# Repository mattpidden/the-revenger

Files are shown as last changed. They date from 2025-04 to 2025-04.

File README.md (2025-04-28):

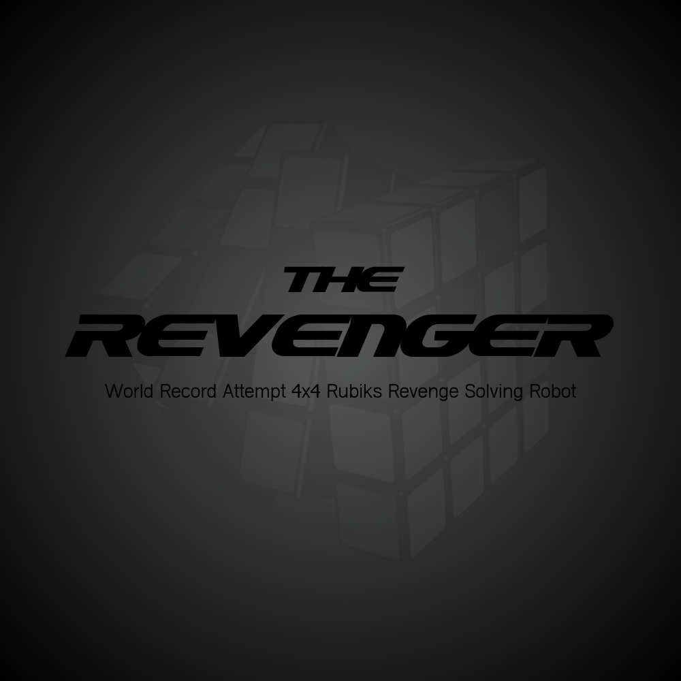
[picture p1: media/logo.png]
Banner Photo







# The Revenger - 4x4 Rubik’s Cube Solving Robot

This project presents the development of an efficient computational solver for the 4x4 Rubik's Cube and its implementation within a robotic system that achieves a world record solving time.

The approach uses a 2D array of integer facelet identifiers, which is the most suitable data structure for the 4x4 Rubik's Cube. This data structure is used in an 8 phase solving algorithm inspired by Tsai's method, and presented as the first C++ implementation of its kind. The approach is original yet closely based on Tsai's framework, offering a unique variation that prioritises practicality and performance. The 8 phase method achieves short solutions with an average move count of 67.79 moves in near real time. Additionally, novel research was conducted into optimising a computational solver to the characteristics and constraints of a specific robotic system, an area that has not been previously explored in existing literature. Unlike existing 4x4 solvers, this project is the only one accompanied by any explanation of the underlying theory and implementation, making it the first truly transparent and practical resource for 4x4 computational solving. The robot was designed and constructed from the ground up using fully custom parts and original architecture, independent of existing designs. The integration of the computational solver and robotic system achieved a solve time of 47.93 seconds, a 39.08% improvement over the current official world record. 

These results demonstrate that the robot, named 'The Revenger', has achieved an unofficial new world record time for solving the 4x4 Rubik's Cube. In due course the evidence will be submitted to Guinness World Records for review of official recognition.

A video demonstration of the robot is available on [YouTube](https://youtu.be/tE4DD7Fw6SM).

# Project Structure
```
code/ 
  solver/
  scanner/ 
  master/
  microcontroller/ 
parts/
  pcb/
media/
```

# Instructions
To run the 8 phase solver, first download the latest binary assets from [here](https://github.com/mattpidden/the-revenger/releases) and place them in the `code/solver` directory. Then type `make` to generate the compiled solver. Run `./solver -s` to solve a cube. It expects a 96 char input of the inital cube state.

To run the master program use `python main.py` inside the `code/master` directory. 

To run the computer vision scanning use `python manual_scan.py` inside the `code/scanner` directory. It is important that you calibrate your cameras first using `python calibrate_cameras.py`.

Upload the microcontroller code to an Arduino using the offical software.

# Parts List
Along with the parts provided that you will need to 3D print, there are also a selection of parts to source from elsewhere.
- Custom PCB (see files) (1 pcs)
- 360x20x20mm extrusion (14 pcs)
- 480x20x20mm extrusion (4 pcs)
- 150x20x20mm extrusion (5 pcs)
- 200x20x20mm extrusion (1 pcs)
- MGN12 100mm linear rail (5 pcs)
- MGN12 150mm linear rail (1 pcs)
- MGN12H sliding carriage blocks (6 pcs)
- Corner connections for 20x20mm extrusion
- 2GTx160x6mm timing belt (6 pcs)
- 2GTx6mm spool timing belt
- 2GT pulley, 20 teeth, 5mm bore (6 pcs)
- 2GT idler, 5mm bore (6 pcs)
- 2GT pulley, 40 teeth, 12mm bore, 28mm dia (4 pcs)
- 2GT pulley, 40 teeth, 5mm bore, 30mm dia (4 pcs)
- NEMA 17 0.65 Nm stepper motor (6 pcs)
- NEMA 17 0.45 Nm stepper motor (4 pcs)
- Endstop mechanical limit switch (6 pcs)
- 2 Lenovo Essential FHD webameras
- Arduino Due (1 pcs)
- DRV8825 stepper motor driver (10 pcs)
- TM1637 4 digit 7 segment display (1 pcs)
- DC buzzer (1 pcs)
- LED ring light (2 pcs)
- Capacitors
- Male and female header pins

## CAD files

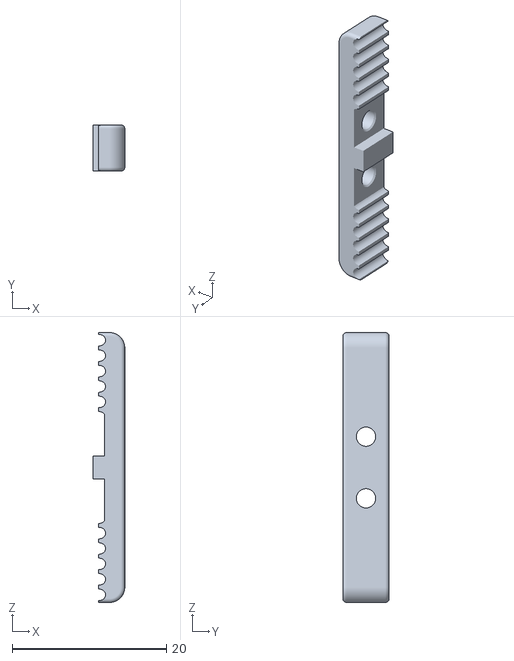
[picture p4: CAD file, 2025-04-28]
parts/4x4 Solver PRT_103-3-010325 - LA Inner Belt Joiner.STL
4.10 x 6.00 x 35.0

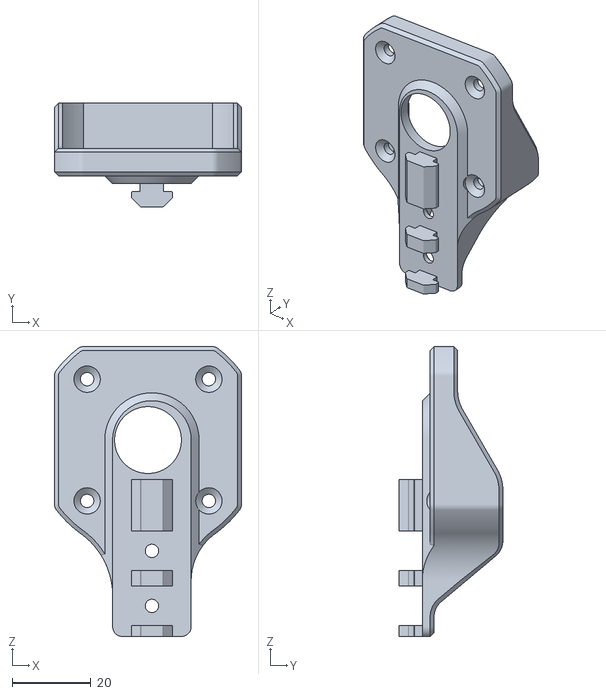
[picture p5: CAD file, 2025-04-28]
parts/4x4 Solver PRT_101-4-040325 - LA Motor Mount.STL
47.6 x 26.4 x 73.8

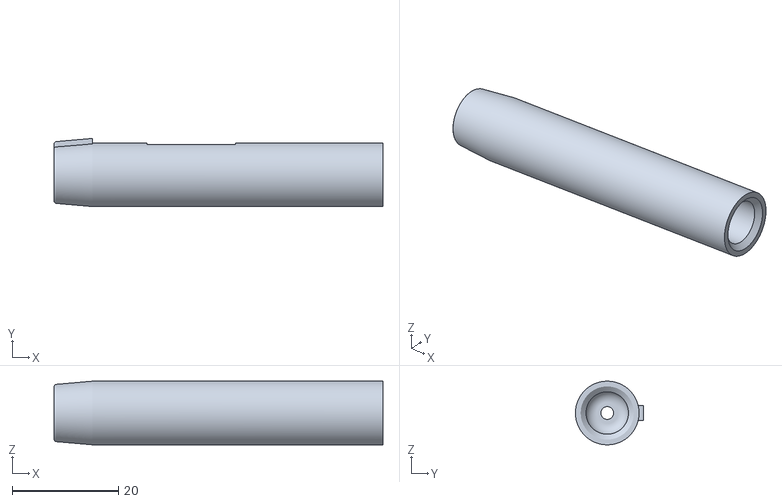
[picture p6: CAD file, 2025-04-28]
parts/4x4 Solver PRT_002-4-080325 - Claw Axel.STL
62.0 x 12.9 x 12.0

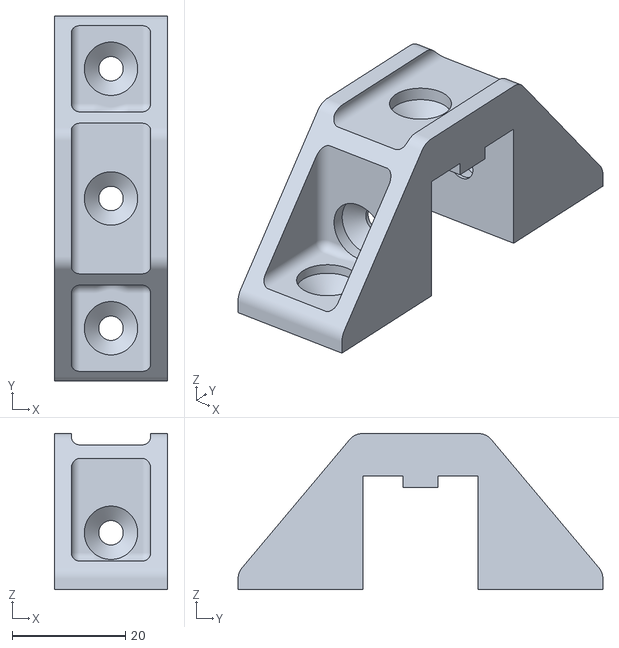
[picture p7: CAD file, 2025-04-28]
parts/4x4 Solver PRT_302-4-060325 - LA Frame Mount B.STL
20.0 x 64.3 x 27.5

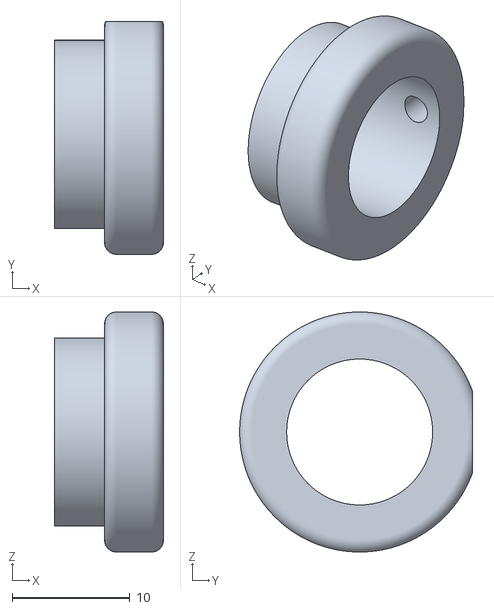
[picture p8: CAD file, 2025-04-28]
parts/4x4 Solver PRT_005-3-010325 - Axel Stopper.STL
9.25 x 19.8 x 20.4

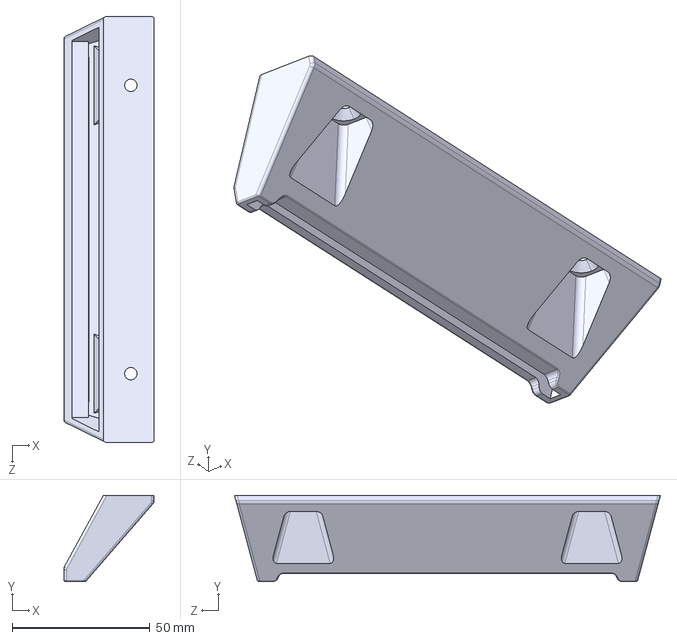
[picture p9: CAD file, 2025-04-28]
parts/4x4 Solver PRT_313-1-260325 - PCB Mount.STEP
32.9 x 31.2 x 154.7 mm

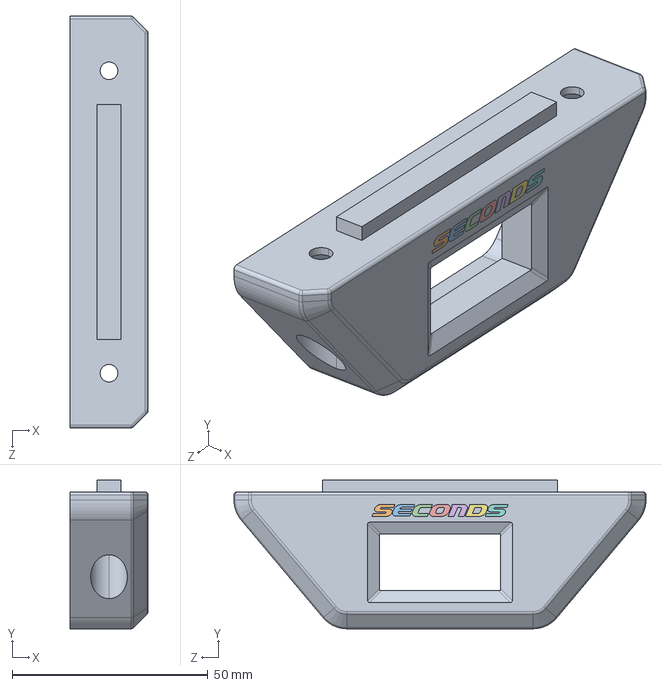
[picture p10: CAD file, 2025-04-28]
parts/4x4 Solver PRT_309--1-031025 - Clock Mount.STEP
20.0 x 38.0 x 105.3 mm

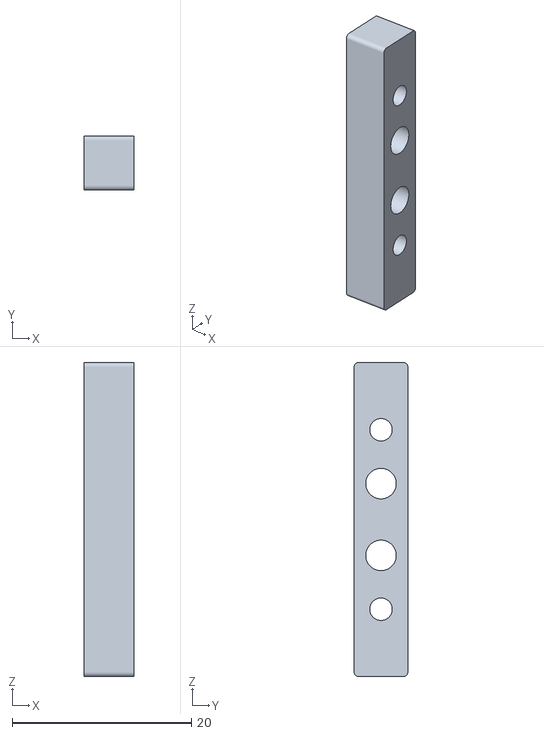
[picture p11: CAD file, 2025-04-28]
parts/4x4 Solver PRT_104-3-010325 - LA Outer Belt Joiner.STL
5.52 x 6.00 x 35.0

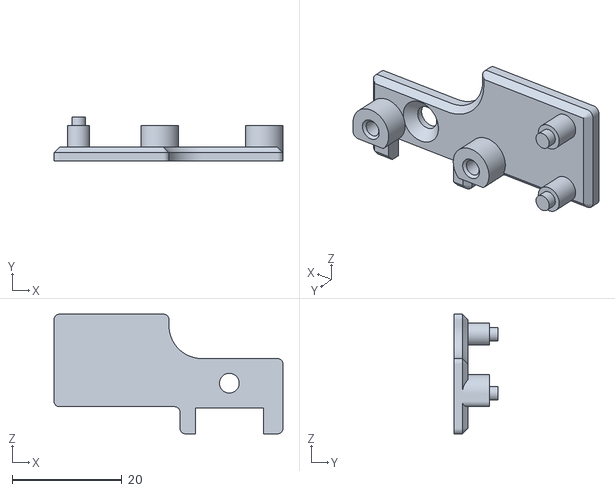
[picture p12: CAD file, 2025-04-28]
parts/4x4 Solver PRT_105-3-010325 - LA Switch Mount.STL
41.8 x 8.00 x 21.8

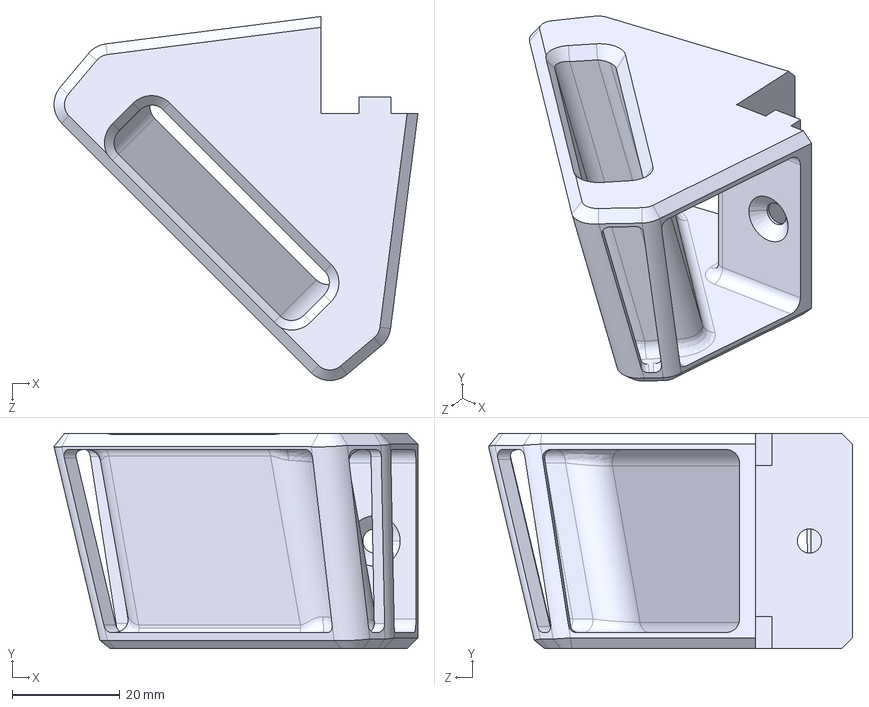
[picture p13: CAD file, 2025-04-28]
parts/4x4 Solver PRT_310-2-260325 - Camera clip.STEP
67.6 x 40.0 x 67.6 mm

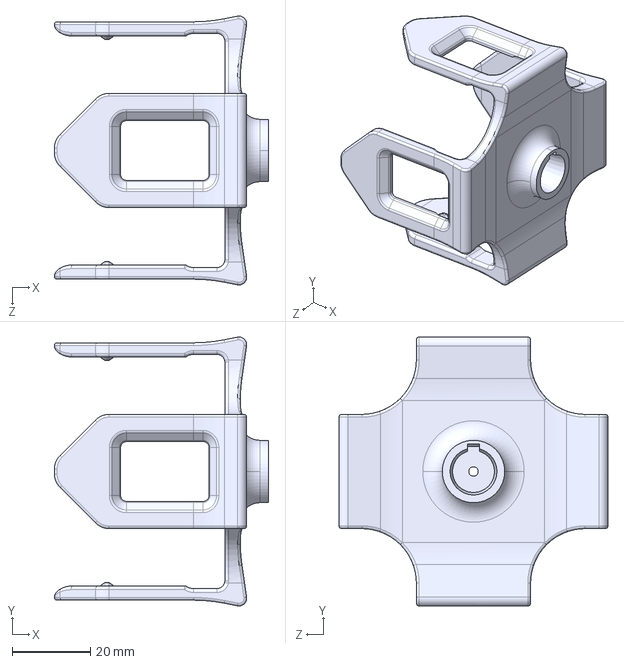
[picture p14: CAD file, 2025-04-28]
parts/4x4 Solver PRT_001-4-220425 - Claw.STEP
54.9 x 69.0 x 69.0 mm

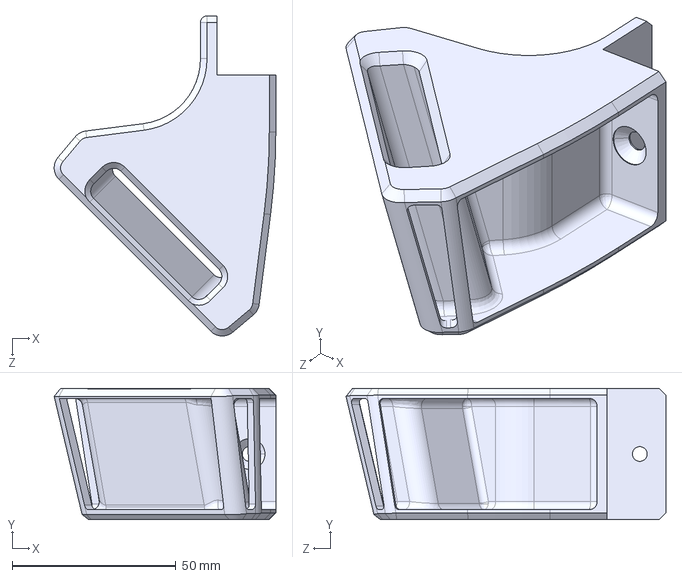
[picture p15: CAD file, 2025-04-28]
parts/4x4 Solver PRT_311-1-260325 - Camera clip B.STEP
67.6 x 40.0 x 97.6 mm

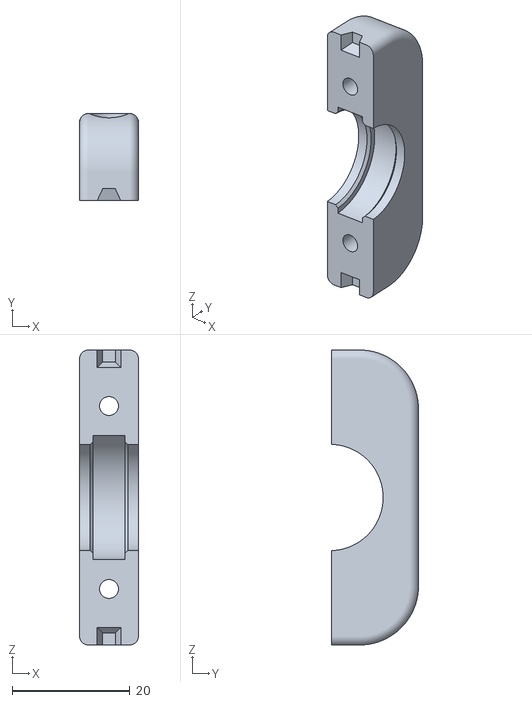
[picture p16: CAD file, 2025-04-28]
parts/4x4 Solver PRT_004-3-010325 - Bearing Cap.STL
10.00 x 14.8 x 50.0

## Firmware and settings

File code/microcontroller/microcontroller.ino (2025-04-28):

#include <AccelStepper.h>
#include <array>
#include "TM1637.h"

// ***************************************************
// ********************* PINS ************************
// ***************************************************
#define x_axis_1_la_dir 23
#define x_axis_1_la_step 30
#define x_axis_1_la_enable 13
#define x_axis_1_la_limit 32

#define x_axis_2_la_dir 25
#define x_axis_2_la_step 28
#define x_axis_2_la_enable 10
#define x_axis_2_la_limit 34

#define z_axis_1_la_dir 27
#define z_axis_1_la_step 26
#define z_axis_1_la_enable 9
#define z_axis_1_la_limit 40

#define z_axis_2_la_dir 29
#define z_axis_2_la_step 24
#define z_axis_2_la_enable 8
#define z_axis_2_la_limit 42

#define y_axis_1_la_dir 31
#define y_axis_1_la_step 22
#define y_axis_1_la_enable 33
#define y_axis_1_la_limit 36

#define y_axis_2_la_dir 53
#define y_axis_2_la_step 52
#define y_axis_2_la_enable 41
#define y_axis_2_la_limit 38

#define x_axis_1_claw_dir 5
#define x_axis_1_claw_step 6
#define x_axis_1_claw_enable 39

#define x_axis_2_claw_dir 15
#define x_axis_2_claw_step 14
#define x_axis_2_claw_enable 37

#define z_axis_1_claw_dir 49
#define z_axis_1_claw_step 48
#define z_axis_1_claw_enable 35

#define z_axis_2_claw_dir 51
#define z_axis_2_claw_step 50
#define z_axis_2_claw_enable 43

#define buzzer_pin 7
#define display_clock_pin 2
#define display_dio_pin 3




// ***************************************************
// **************** INITALISATION ********************
// ***************************************************
TM1637 digit_display(display_clock_pin, display_dio_pin);

struct LinearMotor {
    AccelStepper* stepper;
    int limit_pin;
    int enable_pin;
};

struct ClawMotor {
    AccelStepper* stepper;
    int enable_pin;
};

#define motorInterfaceType 1

AccelStepper x_axis_1_la_stepper(motorInterfaceType, x_axis_1_la_step, x_axis_1_la_dir);
AccelStepper x_axis_2_la_stepper(motorInterfaceType, x_axis_2_la_step, x_axis_2_la_dir);
AccelStepper z_axis_1_la_stepper(motorInterfaceType, z_axis_1_la_step, z_axis_1_la_dir);
AccelStepper z_axis_2_la_stepper(motorInterfaceType, z_axis_2_la_step, z_axis_2_la_dir);
AccelStepper y_axis_1_la_stepper(motorInterfaceType, y_axis_1_la_step, y_axis_1_la_dir);
AccelStepper y_axis_2_la_stepper(motorInterfaceType, y_axis_2_la_step, y_axis_2_la_dir);

AccelStepper x_axis_1_claw_stepper(motorInterfaceType, x_axis_1_claw_step, x_axis_1_claw_dir);
AccelStepper x_axis_2_claw_stepper(motorInterfaceType, x_axis_2_claw_step, x_axis_2_claw_dir);
AccelStepper z_axis_1_claw_stepper(motorInterfaceType, z_axis_1_claw_step, z_axis_1_claw_dir);
AccelStepper z_axis_2_claw_stepper(motorInterfaceType, z_axis_2_claw_step, z_axis_2_claw_dir);

LinearMotor x_axis_1_la = {&x_axis_1_la_stepper, x_axis_1_la_limit, x_axis_1_la_enable};
LinearMotor x_axis_2_la = {&x_axis_2_la_stepper, x_axis_2_la_limit, x_axis_2_la_enable};
LinearMotor z_axis_1_la = {&z_axis_1_la_stepper, z_axis_1_la_limit, z_axis_1_la_enable};
LinearMotor z_axis_2_la = {&z_axis_2_la_stepper, z_axis_2_la_limit, z_axis_2_la_enable};
LinearMotor y_axis_1_la = {&y_axis_1_la_stepper, y_axis_1_la_limit, y_axis_1_la_enable};
LinearMotor y_axis_2_la = {&y_axis_2_la_stepper, y_axis_2_la_limit, y_axis_2_la_enable};

ClawMotor x_axis_1_claw = {&x_axis_1_claw_stepper, x_axis_1_claw_enable};
ClawMotor x_axis_2_claw = {&x_axis_2_claw_stepper, x_axis_2_claw_enable};
ClawMotor z_axis_1_claw = {&z_axis_1_claw_stepper, z_axis_1_claw_enable};
ClawMotor z_axis_2_claw = {&z_axis_2_claw_stepper, z_axis_2_claw_enable};




// ***************************************************
// ****************** CONSTANTS **********************
// ***************************************************
std::array<LinearMotor, 6> la_motors = {x_axis_1_la, x_axis_2_la, z_axis_1_la, z_axis_2_la, y_axis_1_la, y_axis_2_la};
std::array<LinearMotor, 4> la_hub_motors = {x_axis_1_la, x_axis_2_la, z_axis_1_la, z_axis_2_la};
std::array<LinearMotor, 2> la_cg_motors = {y_axis_1_la, y_axis_2_la};
std::array<ClawMotor, 4> claw_motors = {x_axis_1_claw, x_axis_2_claw, z_axis_1_claw, z_axis_2_claw};

int steps_per_revolution = 200;
float pulley_circumfrence = 40.0;
float steps_per_mm = steps_per_revolution / pulley_circumfrence;

float linear_rail_distance = 62.2;
float depth_0_distance = 10.0;
float depth_1_distance = 33.6; 
float depth_2_distance = 47.2;
float depth_3_distance = 61.0;
float corner_grabber_engaged_distance = 56.5;
float corner_grabber_disengaged_distance = 42.0;

int depth_0_position = depth_0_distance * steps_per_mm;
int depth_1_position = depth_1_distance * steps_per_mm;
int depth_2_position = depth_2_distance * steps_per_mm;
int depth_3_position = depth_3_distance * steps_per_mm;
float corner_grabber_engaged_position = corner_grabber_engaged_distance * steps_per_mm;
float corner_grabber_disengaged_position = corner_grabber_disengaged_distance * steps_per_mm;

float linear_motor_max_speed = 40000.0;
float claw_motor_max_speed = 40000.0;
float linear_motor_acceleration = 8000.0;
float claw_motor_acceleration = 8000.0;





// ***************************************************
// ********************* SETUP ***********************
// ***************************************************
void setup() {
  Serial.begin(9600); 

  pinMode(x_axis_1_la_dir, OUTPUT); 
  pinMode(x_axis_1_la_step, OUTPUT); 
  pinMode(x_axis_2_la_dir, OUTPUT); 
  pinMode(x_axis_2_la_step, OUTPUT);
  pinMode(z_axis_1_la_dir, OUTPUT); 
  pinMode(z_axis_1_la_step, OUTPUT); 
  pinMode(z_axis_2_la_dir, OUTPUT); 
  pinMode(z_axis_2_la_step, OUTPUT); 
  pinMode(y_axis_1_la_dir, OUTPUT); 
  pinMode(y_axis_1_la_step, OUTPUT); 
  pinMode(y_axis_2_la_dir, OUTPUT); 
  pinMode(y_axis_2_la_step, OUTPUT); 
  pinMode(x_axis_1_claw_dir, OUTPUT); 
  pinMode(x_axis_1_claw_step, OUTPUT); 
  pinMode(x_axis_2_claw_dir, OUTPUT); 
  pinMode(x_axis_2_claw_step, OUTPUT); 
  pinMode(z_axis_1_claw_dir, OUTPUT); 
  pinMode(z_axis_1_claw_step, OUTPUT); 
  pinMode(z_axis_2_claw_dir, OUTPUT); 
  pinMode(z_axis_2_claw_step, OUTPUT); 
  
  pinMode(x_axis_1_la_enable, OUTPUT); 
  pinMode(x_axis_2_la_enable, OUTPUT); 
  pinMode(z_axis_1_la_enable, OUTPUT); 
  pinMode(z_axis_2_la_enable, OUTPUT); 
  pinMode(y_axis_1_la_enable, OUTPUT); 
  pinMode(y_axis_2_la_enable, OUTPUT); 
  pinMode(x_axis_1_claw_enable, OUTPUT); 
  pinMode(x_axis_2_claw_enable, OUTPUT); 
  pinMode(z_axis_1_claw_enable, OUTPUT); 
  pinMode(z_axis_2_claw_enable, OUTPUT); 
  pinMode(x_axis_1_la_limit, INPUT_PULLUP); 
  pinMode(x_axis_2_la_limit, INPUT_PULLUP); 
  pinMode(z_axis_1_la_limit, INPUT_PULLUP); 
  pinMode(z_axis_2_la_limit, INPUT_PULLUP); 
  pinMode(y_axis_1_la_limit, INPUT_PULLUP); 
  pinMode(y_axis_2_la_limit, INPUT_PULLUP); 
  pinMode(buzzer_pin, OUTPUT);
  
  digitalWrite(x_axis_1_la_enable, HIGH);
  digitalWrite(x_axis_2_la_enable, HIGH);
  digitalWrite(z_axis_1_la_enable, HIGH);
  digitalWrite(z_axis_2_la_enable, HIGH);
  digitalWrite(y_axis_1_la_enable, HIGH);
  digitalWrite(y_axis_2_la_enable, HIGH);
  digitalWrite(x_axis_1_claw_enable, HIGH);
  digitalWrite(x_axis_2_claw_enable, HIGH);
  digitalWrite(z_axis_1_claw_enable, HIGH);
  digitalWrite(z_axis_2_claw_enable, HIGH);

  for (LinearMotor &motor : la_motors) {
    motor.stepper->setMaxSpeed(linear_motor_max_speed);
    motor.stepper->setAcceleration(linear_motor_acceleration);
  }
  for (ClawMotor &motor : claw_motors) {
    motor.stepper->setMaxSpeed(claw_motor_max_speed);
    motor.stepper->setAcceleration(claw_motor_acceleration);
  }

  digit_display.init();
  digit_display.set(2);
  updateDisplay(micros(), micros());
  soundBuzzer();

}




// ***************************************************
// ******************* MAIN LOOP *********************
// ***************************************************
bool timer = false;
unsigned long start_time = micros(); 

void loop() {
  updateDisplay(start_time, micros());

  static String command = "";

  while (Serial.available() > 0) {
    char incoming_char = Serial.read();

    if (incoming_char == '\n' || incoming_char == '\r') {
      if (command.length() > 0) {
        apply_command(command);
        command = "";
      }
    } else {
      command += incoming_char;
    }
  }
}

void apply_command(String command) {
  if (command == "c") {
    calibrateLinearAcctuators(); 
  }
  else if (command == "C") {
    calibrateLinearAcctuatorsWithCube(); 
  }
  else if (command == "CY") {
    calibrateCornerGrabbers(); 
  }
  else if (command == "S") {
    move2LinearHub(y_axis_1_la, y_axis_2_la, corner_grabber_engaged_position, corner_grabber_engaged_position);
  }
  else if (command == "N") {
    soundBuzzer(); 
  }
  else if (command =="T") {
    timer = !timer;
    soundBuzzer(); 
    start_time = micros(); 
  }
  else if (command == "S1") {
    float linear_motor_max_speed = 40000.0;
    float claw_motor_max_speed = 40000.0;
    float linear_motor_acceleration = 8000.0;
    float claw_motor_acceleration = 8000.0;
    for (LinearMotor &motor : la_motors) {
      motor.stepper->setMaxSpeed(linear_motor_max_speed);
      motor.stepper->setAcceleration(linear_motor_acceleration);
    }
    for (ClawMotor &motor : claw_motors) {
      motor.stepper->setMaxSpeed(claw_motor_max_speed);
      motor.stepper->setAcceleration(claw_motor_acceleration);
    }
  }
  else if (command == "S2") {
    float linear_motor_max_speed = 60000.0;
    float claw_motor_max_speed = 60000.0;
    float linear_motor_acceleration = 20000.0;
    float claw_motor_acceleration = 20000.0;
    for (LinearMotor &motor : la_motors) {
      motor.stepper->setMaxSpeed(linear_motor_max_speed);
      motor.stepper->setAcceleration(linear_motor_acceleration);
    }
    for (ClawMotor &motor : claw_motors) {
      motor.stepper->setMaxSpeed(claw_motor_max_speed);
      motor.stepper->setAcceleration(claw_motor_acceleration);
    }
  }
  else if (command == "S3") {
    float linear_motor_max_speed = 80000.0;
    float claw_motor_max_speed = 80000.0;
    float linear_motor_acceleration = 60000.0;
    float claw_motor_acceleration = 35000.0;
    for (LinearMotor &motor : la_motors) {
      motor.stepper->setMaxSpeed(linear_motor_max_speed);
      motor.stepper->setAcceleration(linear_motor_acceleration);
    }
    for (ClawMotor &motor : claw_motors) {
      motor.stepper->setMaxSpeed(claw_motor_max_speed);
      motor.stepper->setAcceleration(claw_motor_acceleration);
    }
  }
  else if (command == "SPIN") {
    Serial.println(command);
    enableClaws(x_axis_1_claw, x_axis_2_claw);
    enableClaws(z_axis_1_claw, z_axis_2_claw);
    x_axis_1_claw.stepper->move(200 * 30);
    x_axis_2_claw.stepper->move(200 * 30);
    z_axis_1_claw.stepper->move(200 * 30);
    z_axis_2_claw.stepper->move(200 * 30);
    while (x_axis_1_claw.stepper->distanceToGo() != 0 || x_axis_2_claw.stepper->distanceToGo() != 0 || z_axis_1_claw.stepper->distanceToGo() != 0 || z_axis_2_claw.stepper->distanceToGo() != 0) {
      x_axis_1_claw.stepper->run();
      x_axis_2_claw.stepper->run();
      z_axis_1_claw.stepper->run();
      z_axis_2_claw.stepper->run();
    }
    disableClaws(x_axis_1_claw, x_axis_2_claw);
    disableClaws(z_axis_1_claw, z_axis_2_claw);
    return;
  }
  else if (command == "A") {
    adjustCornerGrabbers();
  }
  else if (command == "0") {
    move2LinearHub(x_axis_2_la, x_axis_1_la, depth_0_position, depth_0_position);
    move2LinearHub(z_axis_2_la, z_axis_1_la, depth_0_position, depth_0_position);
  }
  else if (command == "00") {
    move2LinearHub(x_axis_2_la, x_axis_1_la, 0, 0);
    move2LinearHub(z_axis_2_la, z_axis_1_la, 0, 0);
  }
  else if (command == "1") {
    move2LinearHub(x_axis_2_la, x_axis_1_la, depth_0_position, depth_2_position);
  }
  else if (command == "2") {
    move2LinearHub(x_axis_2_la, x_axis_1_la, depth_2_position, depth_2_position);
  }
  else if (command == "3") {
    move2LinearHub(x_axis_2_la, x_axis_1_la, depth_3_position, depth_1_position);
  }
  else if (command == "4") {
    move2LinearHub(z_axis_1_la, z_axis_2_la, depth_0_position, depth_0_position);
  }
  else if (command == "5") {
    move2LinearHub(z_axis_1_la, z_axis_2_la, depth_1_position, depth_3_position);
  }
  else if (command == "6") {
    move2LinearHub(z_axis_1_la, z_axis_2_la, depth_2_position, depth_2_position);
  }
  else if (command == "7") {
    move2LinearHub(z_axis_1_la, z_axis_2_la, depth_3_position, depth_1_position);
  }
  else if (command == "8") {
    move2LinearHub(y_axis_1_la, y_axis_2_la, corner_grabber_disengaged_position, corner_grabber_disengaged_position);
  }
  else if (command == "9") {
    move2LinearHub(y_axis_1_la, y_axis_2_la, corner_grabber_engaged_position, corner_grabber_engaged_position);
  }
  else if (command != "") {
    apply_move(command);
  }
  Serial.println(command);
}



// ***************************************************
// **************** OTHER FUNCTIONS ******************
// ***************************************************
void soundBuzzer() {
  digitalWrite(buzzer_pin, HIGH);
  delay(100);
  digitalWrite(buzzer_pin, LOW);
}

void updateDisplay(unsigned long startTime, unsigned long endTime) {
  if (timer) {
    unsigned long durationMicroseconds = endTime - startTime;
    float durationMilliseconds = durationMicroseconds / 1000.0;
    float durationSeconds = durationMicroseconds / 1000000.0;
    int totalSeconds = (int)durationSeconds;
    int minutes = totalSeconds / 60;
    int seconds = totalSeconds % 60;
    int hundredths = ((int)durationMilliseconds % 1000) / 10;
    int8_t displayValues[4];
    if (totalSeconds >= 60) {
      displayValues[0] = static_cast<int8_t>(minutes / 10);
      displayValues[1] = static_cast<int8_t>(minutes % 10);
      displayValues[2] = static_cast<int8_t>(seconds / 10);
      displayValues[3] = static_cast<int8_t>(seconds % 10);
    } else {
      displayValues[0] = static_cast<int8_t>(totalSeconds / 10);
      displayValues[1] = static_cast<int8_t>(totalSeconds % 10);
      displayValues[2] = static_cast<int8_t>(hundredths / 10);
      displayValues[3] = static_cast<int8_t>(hundredths % 10);
    }
    digit_display.point(POINT_ON);
    digit_display.display(displayValues);
  }
}


void resetDisplay() {
  digit_display.clearDisplay();
  digit_display.point(POINT_OFF);
}

void calibrateLinearAcctuators() {
  for (LinearMotor &motor : la_motors) {
    digitalWrite(motor.enable_pin, LOW);
    while (digitalRead(motor.limit_pin) == HIGH) { 
      motor.stepper->move(-1); 
      motor.stepper->run();
      delay(10);
    }
    motor.stepper->stop();
    motor.stepper->setCurrentPosition(0);
    motor.stepper->moveTo(depth_0_position);
    motor.stepper->runToPosition();
    digitalWrite(motor.enable_pin, HIGH);
  }
  moveLinearHub(y_axis_2_la, corner_grabber_engaged_position);
}

void calibrateLinearAcctuatorsWithCube() {
  for (LinearMotor &motor : la_hub_motors) {
    digitalWrite(motor.enable_pin, LOW);
    while (digitalRead(motor.limit_pin) == HIGH) { 
      motor.stepper->move(-1); 
      motor.stepper->run();
      delay(10);
    }
    motor.stepper->stop();
    motor.stepper->setCurrentPosition(0);
    motor.stepper->moveTo(depth_0_position);
    motor.stepper->runToPosition();
    digitalWrite(motor.enable_pin, HIGH);
  }
  move2LinearHub(x_axis_1_la, x_axis_2_la, depth_2_position, depth_2_position);
  calibrateCornerGrabbers();
  move2LinearHub(x_axis_1_la, x_axis_2_la, depth_0_position, depth_0_position);
}

void calibrateCornerGrabbers() {
  for (LinearMotor &motor : la_cg_motors) {
    digitalWrite(motor.enable_pin, LOW);
    while (digitalRead(motor.limit_pin) == HIGH) { 
      motor.stepper->move(-1); 
      motor.stepper->run();
      delay(10);
    }
    motor.stepper->stop();
    motor.stepper->setCurrentPosition(0);
    digitalWrite(motor.enable_pin, HIGH);
  }
  move2LinearHub(y_axis_1_la, y_axis_2_la, corner_grabber_engaged_position, corner_grabber_engaged_position);
}

void moveLinearHub(LinearMotor motor, int position) {
  updateDisplay(start_time, micros());
  digitalWrite(motor.enable_pin, LOW);
  motor.stepper->moveTo(position);
  motor.stepper->runToPosition();
  digitalWrite(motor.enable_pin, HIGH);
}

void move2LinearHub(LinearMotor motor1, LinearMotor motor2, int position1, int position2) {
  updateDisplay(start_time, micros());
  digitalWrite(motor1.enable_pin, LOW);
  digitalWrite(motor2.enable_pin, LOW);
  motor1.stepper->moveTo(position1);
  motor2.stepper->moveTo(position2);
  while (motor1.stepper->distanceToGo() != 0 || motor2.stepper->distanceToGo() != 0) {
    motor1.stepper->run();
    motor2.stepper->run();
  }
  digitalWrite(motor1.enable_pin, HIGH);
  digitalWrite(motor2.enable_pin, HIGH);
}

void adjustCornerGrabbers() {
  digitalWrite(y_axis_1_la.enable_pin, LOW);
  digitalWrite(y_axis_2_la.enable_pin, LOW);
  y_axis_2_la.stepper->move(5);
  y_axis_2_la.stepper->runToPosition();
  digitalWrite(y_axis_1_la.enable_pin, HIGH);
  digitalWrite(y_axis_2_la.enable_pin, HIGH);
}

void enableClaws(ClawMotor claw1, ClawMotor claw2) {
  updateDisplay(start_time, micros());
  digitalWrite(claw1.enable_pin, LOW);
  digitalWrite(claw2.enable_pin, LOW);
}

void disableClaws(ClawMotor claw1, ClawMotor claw2) {
  updateDisplay(start_time, micros());
  digitalWrite(claw1.enable_pin, HIGH);
  digitalWrite(claw2.enable_pin, HIGH);
}

void rotateClaw(ClawMotor active_claw, int turns) {
  updateDisplay(start_time, micros());
  active_claw.stepper->move(50 * turns);
  while (active_claw.stepper->distanceToGo() != 0) {
    active_claw.stepper->run();
  }
}

void rotate2Claws(ClawMotor claw1, ClawMotor claw2, int turns) {
  updateDisplay(start_time, micros());
  claw1.stepper->move(50 * turns);
  claw2.stepper->move(50 * turns);
  while (claw1.stepper->distanceToGo() != 0 || claw2.stepper->distanceToGo() != 0) {
    claw1.stepper->run();
    claw2.stepper->run();
  }
}




// ***************************************************
// **************** MOVE FUNCTIONS *******************
// ***************************************************

void apply_move(String m) {
  if      (m == "R")   R_move(1); 
  else if (m == "R2")  R_move(2);
  else if (m == "R'")  R_move(-1);
  else if (m == "L")   L_move(1); 
  else if (m == "L2")  L_move(2);
  else if (m == "L'")  L_move(-1);
  else if (m == "F")   F_move(1); 
  else if (m == "F2")  F_move(2);
  else if (m == "F'")  F_move(-1);
  else if (m == "B")   B_move(1); 
  else if (m == "B2")  B_move(2);
  else if (m == "B'")  B_move(-1);
  else if (m == "U")   U_move(1); 
  else if (m == "U2")  U_move(2);
  else if (m == "U'")  U_move(-1);
  else if (m == "D")   D_move(1); 
  else if (m == "D2")  D_move(2);
  else if (m == "D'")  D_move(-1);
  else if (m == "r")   r_move(1); 
  else if (m == "r2")  r_move(2);
  else if (m == "r'")  r_move(-1);
  else if (m == "l")   l_move(1); 
  else if (m == "l2")  l_move(2);
  else if (m == "l'")  l_move(-1);
  else if (m == "f")   f_move(1); 
  else if (m == "f2")  f_move(2);
  else if (m == "f'")  f_move(-1);
  else if (m == "b")   b_move(1); 
  else if (m == "b2")  b_move(2);
  else if (m == "b'")  b_move(-1);
  else if (m == "u")   u_move(1); 
  else if (m == "u2")  u_move(2);
  else if (m == "u'")  u_move(-1);
  else if (m == "d")   d_move(1); 
  else if (m == "d2")  d_move(2);
  else if (m == "d'")  d_move(-1);
  else if (m == "Rw")  Rw_move(1); 
  else if (m == "Rw2") Rw_move(2);
  else if (m == "Rw'") Rw_move(-1);
  else if (m == "Lw")  Lw_move(1); 
  else if (m == "Lw2") Lw_move(2);
  else if (m == "Lw'") Lw_move(-1);
  else if (m == "Fw")  Fw_move(1); 
  else if (m == "Fw2") Fw_move(2);
  else if (m == "Fw'") Fw_move(-1);
  else if (m == "Bw")  Bw_move(1); 
  else if (m == "Bw2") Bw_move(2);
  else if (m == "Bw'") Bw_move(-1);
  else if (m == "Uw")  Uw_move(1); 
  else if (m == "Uw2") Uw_move(2);
  else if (m == "Uw'") Uw_move(-1);
  else if (m == "Dw")  Dw_move(1); 
  else if (m == "Dw2") Dw_move(2);
  else if (m == "Dw'") Dw_move(-1);
}

void R_move(int turns) {
  move2LinearHub(z_axis_1_la, z_axis_2_la, depth_0_position, depth_0_position);
  move2LinearHub(x_axis_1_la, x_axis_2_la, depth_3_position, depth_1_position);
  enableClaws(x_axis_2_claw, x_axis_1_claw);
  move2LinearHub(y_axis_1_la, y_axis_2_la, corner_grabber_disengaged_position, corner_grabber_disengaged_position);
  rotateClaw(x_axis_2_claw, turns);
  move2LinearHub(y_axis_1_la, y_axis_2_la, corner_grabber_engaged_position, corner_grabber_engaged_position);
  adjustCornerGrabbers();
  disableClaws(x_axis_2_claw, x_axis_1_claw);
}

void L_move(int turns) {
  move2LinearHub(z_axis_1_la, z_axis_2_la, depth_0_position, depth_0_position);
  move2LinearHub(x_axis_1_la, x_axis_2_la, depth_1_position, depth_3_position);
  enableClaws(x_axis_1_claw, x_axis_2_claw);
  move2LinearHub(y_axis_1_la, y_axis_2_la, corner_grabber_disengaged_position, corner_grabber_disengaged_position);
  rotateClaw(x_axis_1_claw, -turns);
  move2LinearHub(y_axis_1_la, y_axis_2_la, corner_grabber_engaged_position, corner_grabber_engaged_position);
  adjustCornerGrabbers();
  disableClaws(x_axis_1_claw, x_axis_2_claw);
}

void F_move(int turns) {
  move2LinearHub(x_axis_1_la, x_axis_2_la, depth_0_position, depth_0_position);
  move2LinearHub(z_axis_1_la, z_axis_2_la, depth_1_position, depth_3_position);
  enableClaws(z_axis_1_claw, z_axis_2_claw);
  move2LinearHub(y_axis_1_la, y_axis_2_la, corner_grabber_disengaged_position, corner_grabber_disengaged_position);
  rotateClaw(z_axis_1_claw, turns);
  move2LinearHub(y_axis_1_la, y_axis_2_la, corner_grabber_engaged_position, corner_grabber_engaged_position);
  adjustCornerGrabbers();
  disableClaws(z_axis_1_claw, z_axis_2_claw);
}
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

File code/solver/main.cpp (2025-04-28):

#include <vector>
#include <limits>
#include <iostream>
#include <fstream>
#include <unordered_map>
#include <functional>
#include <chrono>
#include "cube.h"
#include "BooPHF.h"
using namespace boomphf;

// IDA* recursive search function using table
static bool ida_search_multi(std::vector<Phase> &phases, Cube4x4 &cube, int depth, double &threshold, std::vector<Move> &path, double &next_threshold) {
    double h = 0.0;
    for (Phase &phase : phases) {
        std::string state = phase.mask(cube);
        uint64_t idx = phase.hash_table.lookup(state);
        double phase_h = (idx >= phase.depths.size()) ? (phase.table_depth_limit + 1) : static_cast<double>(static_cast<unsigned char>(phase.depths[idx]));
        h = h + phase_h;
    }

    double f = depth + h;
    if (f > threshold) {
        if (f < next_threshold) {
            next_threshold = f;
        }
        return false;
    }
    if (h == 0) {
        return true;
    }
    if (depth >= phases[0].search_depth_limit) {
        return false;
    }

    Cube4x4 backup = cube;
    for (Move mv : phases[0].moves) {
        cube.move(mv);
        path.push_back(mv);

        if (ida_search_multi(phases, cube, depth + 1, threshold, path, next_threshold)) {
            return true;
        }
        path.pop_back();
        cube = backup;
    }

    return false;
}

// IDA* recursive search function using table
static bool ida_search(Phase &phase, Cube4x4 &cube, int depth, double &threshold, std::vector<Move> &path, double &next_threshold) {
    std::string state = phase.mask(cube);
    uint64_t idx = phase.hash_table.lookup(state);

    double h = (idx >= phase.depths.size()) ? (phase.table_depth_limit + 1) : static_cast<double>(static_cast<unsigned char>(phase.depths[idx]));

    double f = depth + h;
    if (f > threshold) {
        if (f < next_threshold) {
            next_threshold = f;
        }
        return false;
    }
    if (h == 0) {
        return true;
    }
    if (depth >= phase.search_depth_limit) {
        return false;
    }

    Cube4x4 backup = cube;
    for (Move mv : phase.moves) {
        cube.move(mv);
        path.push_back(mv);

        if (ida_search(phase, cube, depth + 1, threshold, path, next_threshold)) {
            return true;
        }
        path.pop_back();
        cube = backup;
    }

    return false;
}

std::vector<Move> solve_any_phase_ida(Phase &phase, Cube4x4 start_cube) {
    std::vector<Move> path;
    std::string state = phase.mask(start_cube);
    uint64_t idx = phase.hash_table.lookup(state);

    double threshold = (idx >= phase.depths.size()) ? (phase.table_depth_limit + 1) : static_cast<double>(static_cast<unsigned char>(phase.depths[idx]));

    while (true) {
        double next_threshold = std::numeric_limits<double>::infinity();
        path.clear();

        bool found = ida_search(phase, start_cube, 0, threshold, path, next_threshold);
        if (found) {
            return path;
        }
        if (next_threshold == std::numeric_limits<double>::infinity()) {
            return {};
        }
        threshold = next_threshold;
    }
}

static bool ida_search_collect(Phase &phase, Cube4x4 &cube, int depth, double &threshold, std::vector<Move> &path, double &next_threshold, int &solutions_found, int max_solutions, std::vector<std::vector<Move>> &all_solutions) {
    std::string state = phase.mask(cube);
    uint64_t idx = phase.hash_table.lookup(state);
    double h = (idx >= phase.depths.size()) ? (phase.table_depth_limit + 1) : static_cast<double>(static_cast<unsigned char>(phase.depths[idx]));
    double f = depth + h;
    if (f > threshold) {
        if (f < next_threshold) { next_threshold = f; }
        return false;
    }
    if (h == 0) {
        all_solutions.push_back(path);
        solutions_found++;
        if (solutions_found >= max_solutions) { return true; }
    }
    if (depth >= phase.search_depth_limit) { return false; }
    Cube4x4 backup = cube;
    for (Move mv : phase.moves) {
        cube.move(mv);
        path.push_back(mv);
        bool filled = ida_search_collect(phase, cube, depth + 1, threshold, path, next_threshold, solutions_found, max_solutions, all_solutions);
        path.pop_back();
        cube = backup;
        if (filled) { return true; }
    }
    return false;
}

std::vector<std::vector<Move>> collect_multiple_solutions(Phase &phase, Cube4x4 start_cube, int how_many) {
    std::vector<std::vector<Move>> solutions;
    solutions.reserve(how_many);
    std::string state = phase.mask(start_cube);
    uint64_t idx = phase.hash_table.lookup(state);
    double threshold = (idx >= phase.depths.size()) ? (phase.table_depth_limit + 1) : static_cast<double>(static_cast<unsigned char>(phase.depths[idx]));
    while ((int)solutions.size() < how_many) {
        double next_threshold = std::numeric_limits<double>::infinity();
        std::vector<Move> path;
        int solutions_found_before = (int)solutions.size();
        ida_search_collect(phase, start_cube, 0, threshold, path, next_threshold, solutions_found_before, how_many, solutions);
        if ((int)solutions.size() == solutions_found_before) {
            if (next_threshold == std::numeric_limits<double>::infinity()) { break; }
            threshold = next_threshold;
        } else {
            if ((int)solutions.size() >= how_many) { break; }
        }
    }
    return solutions;
}

std::vector<char> load_depths(const std::string &filename) {
    std::ifstream in(filename, std::ios::binary);
    uint64_t sz = 0;
    in.read(reinterpret_cast<char*>(&sz), sizeof(sz));
    std::vector<char> depths(sz);
    in.read(reinterpret_cast<char*>(depths.data()), sz);
    return depths;
}

boomphf::mphf<std::string, MyStringHash> load_hash_table(const std::string &filename) {
    boomphf::mphf<std::string, MyStringHash> mph;
    std::ifstream ifs(filename, std::ios::binary);
    mph.load(ifs);
    return mph;
}

int lookup_depth(const std::string &state, const std::string &mph_file, const std::string &depth_file) {
    auto mph = new boomphf::mphf<std::string, MyStringHash>();
    std::ifstream ifs(mph_file, std::ios::binary);
    mph->load(ifs);
    auto depths = load_depths(depth_file);
    uint64_t idx = mph->lookup(state);
    delete mph;
    if (idx >= depths.size()) {
        return -1;
    }
    return depths[idx];
}

static std::pair<double,double> compute_mean_std(const std::vector<double>& vals)
{
    if(vals.empty()) {
        return {0.0, 0.0};
    }
    double sum = 0.0;
    for(double v : vals) {
        sum += v;
    }
    double mean = sum / vals.size();

    double sqSum = 0.0;
    for(double v : vals) {
        double diff = v - mean;
        sqSum += diff * diff;
    }
    double stdev = std::sqrt(sqSum / vals.size());
    return {mean, stdev};
}
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

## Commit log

2025-04-28 Added all parts files
    [4x4 Solver PRT_001-4-220425 - Claw.STEP, 4x4 Solver PRT_002-4-080325 - Claw Axel.STL, 4x4 Solver PRT_004-3-010325 - Bearing Cap.STL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]
2025-04-28 Added pcb files
    [rubiksrobotpcb_contour.gm1, rubiksrobotpcb_copperBottom.gbl, rubiksrobotpcb_copperTop.gtl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]
